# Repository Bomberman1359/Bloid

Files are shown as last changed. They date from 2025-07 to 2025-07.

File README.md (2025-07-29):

# Bloid
This is a custom, ball balancing robot. 

## CAD

Screenshot 2025-07-14 at 4 35 45 AM

## Software

Screenshot 2025-07-14 at 4 37 16 AM

## Software setup

Depending on what device you are on and what directory you export to, the first few steps could vary, so in summary: **you need to ```cd``` into the ```/Software/Main``` folder**

From there, the setup process is very simple:

Create a new python virtual environment:

```
python -m venv env
```

Enter the environment:

```
source env/bin/activate
```

Install the required packages:

```
pip install opencv-python pigpio 
```

Start up the main program:

```
#Start up the pigpio daemon
sudo pigpiod
#Main code
python main.py
```

## Wiring

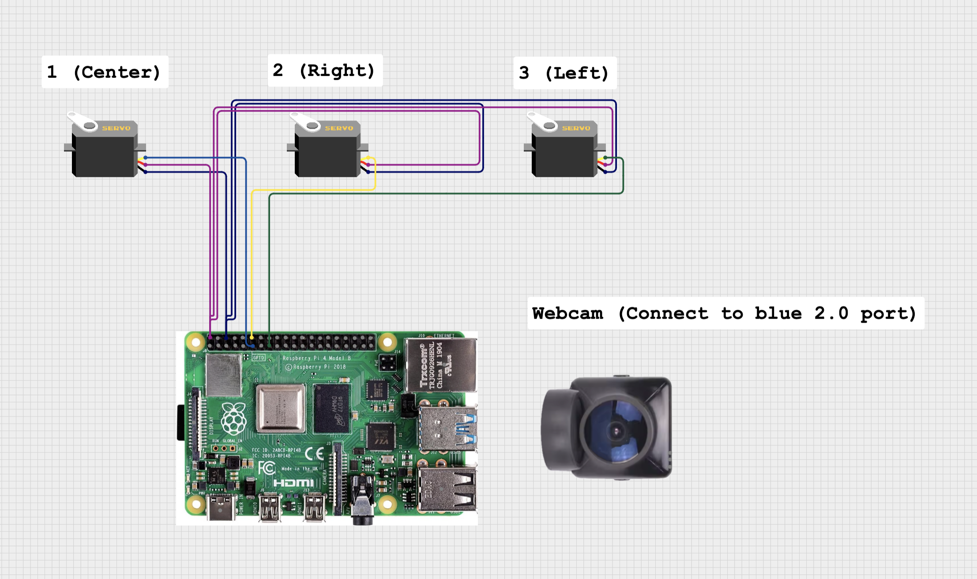
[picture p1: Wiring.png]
Wiring Diagram


## Final Product







## BOM
| Item | Quantity | Vendor | Total Price |
| :--- | :---: | :----- | ---: |
| Raspberry Pi | 1 | [PiShop USA](https://www.pishop.us/product/raspberry-pi-4-model-b-1gb/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) | $35.00 |
| Webcam |  1  |  [Walmart](https://www.walmart.com/ip/1080P-Web-Cam-HD-Camera-Webcam-with-Mic-Microphone-for-Computer-PC-Laptop-Notebook/7115471225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)| $7.99 |
| Servos Set | 1 | [Amazon](https://www.amazon.com/4-Pack-MG996R-Torque-Digital-Helicopter/dp/B07MFK266B?th=1) | $17.99 | 
| M3 Hardware (Set) | 1 | [Amazon](https://www.amazon.com/Taiss-540PCS-Stainless-Socket-Washers/dp/B0D4L6QRZB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) | $9.99 |
| Dupont Wires Set| 1 | [Amazon](https://www.amazon.com/Elegoo-EL-CP-004-Multicolored-Breadboard-arduino/dp/B01EV70C78) | $6.98 |
| 3D Printer and filaments| Undef | Undef | Undef |

Net Total Cost (Not including 3D printer/filaments): $77.95

## Link to the demo:
https://youtu.be/3Ihvu0gQJfA

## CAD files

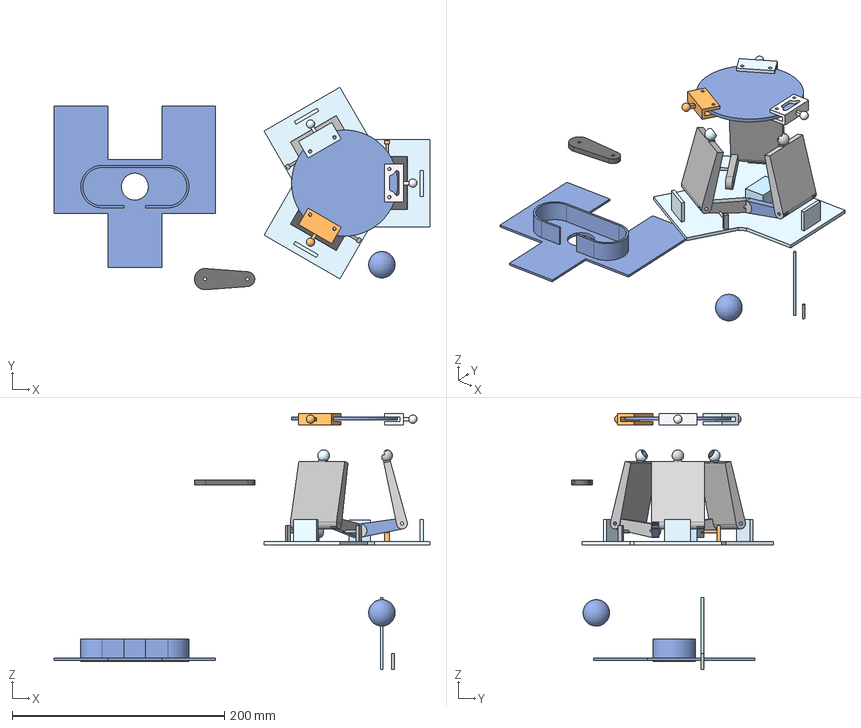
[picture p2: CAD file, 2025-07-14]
CAD/Assembly.step
354.3 x 190.8 x 241.4 mm
arm_2pad

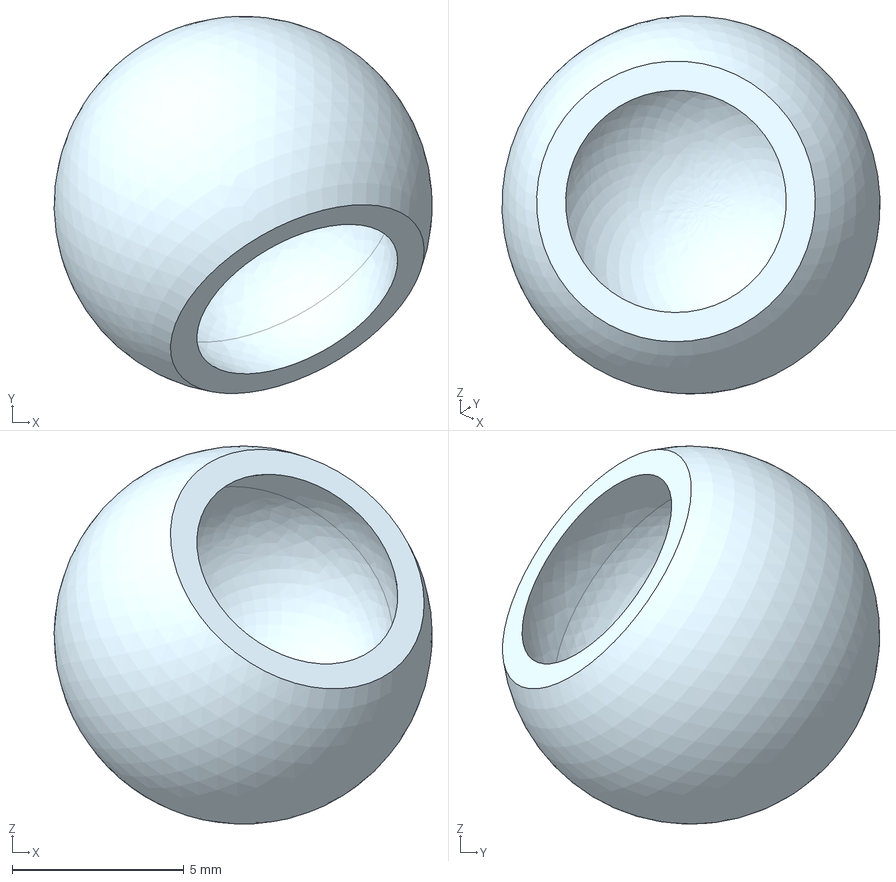
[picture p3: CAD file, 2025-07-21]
CAD/STEP/Part Studio 1 - Part 10.step
11.0 x 11.0 x 11.0 mm

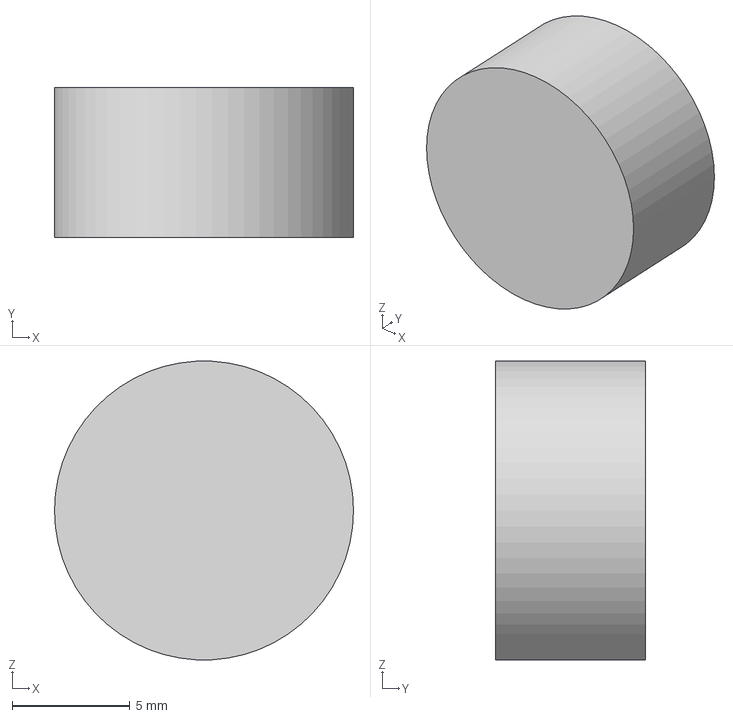
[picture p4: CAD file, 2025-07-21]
CAD/STEP/Part Studio 1 - Part 2.step
12.7 x 6.35 x 12.7 mm

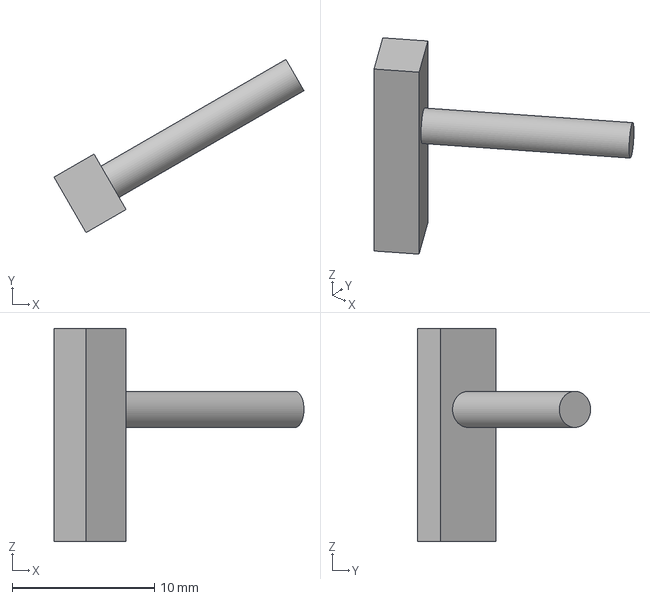
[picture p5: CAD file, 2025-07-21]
CAD/STEP/Part Studio 1 - Part 16.step
17.6 x 12.2 x 15.0 mm

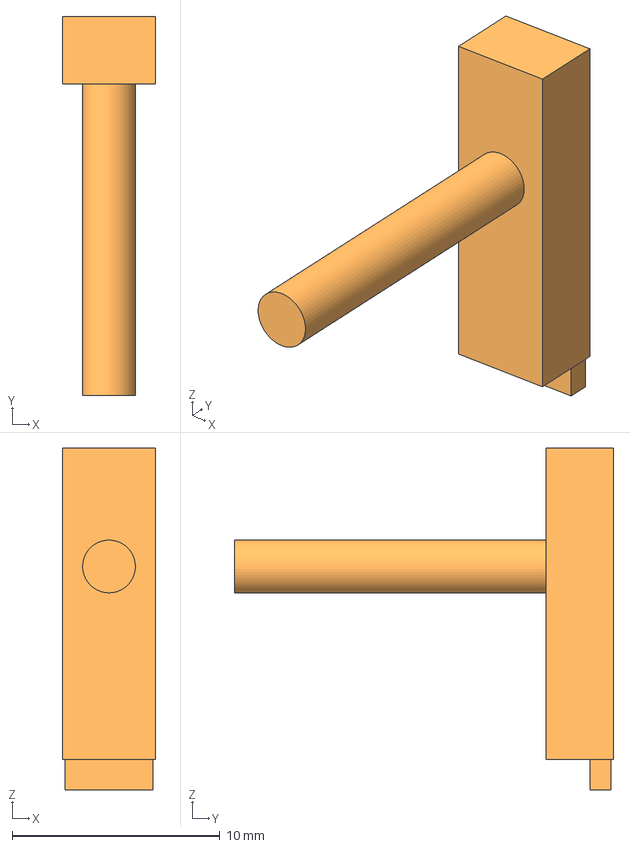
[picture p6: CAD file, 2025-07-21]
CAD/STEP/Part Studio 1 - Part 13.step
4.50 x 18.2 x 16.5 mm

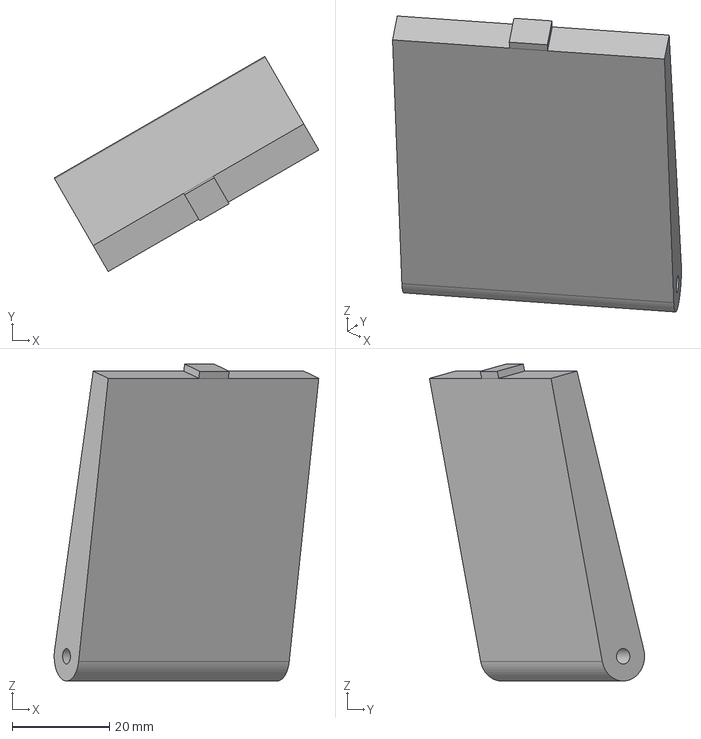
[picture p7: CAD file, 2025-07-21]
CAD/STEP/Part Studio 1 - Part 15.step
54.4 x 44.2 x 65.2 mm

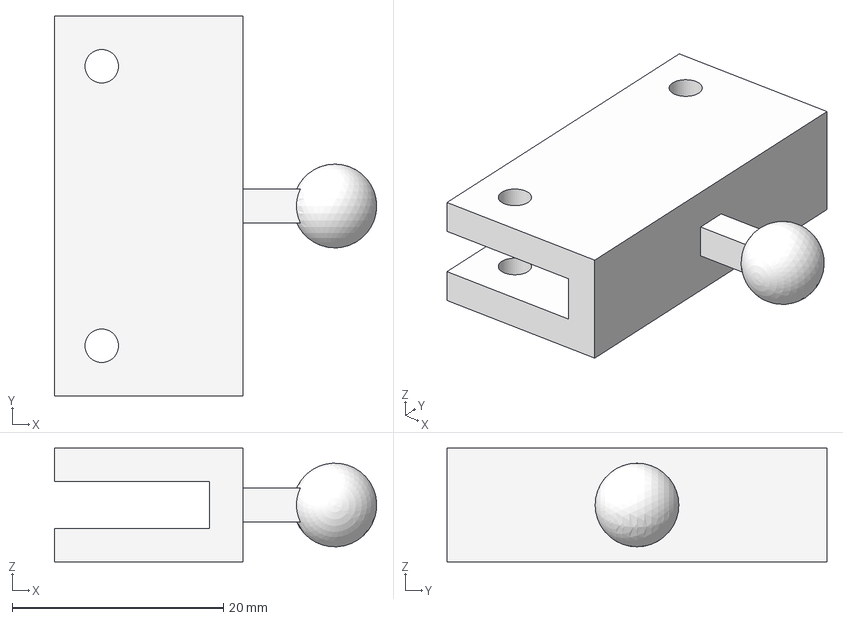
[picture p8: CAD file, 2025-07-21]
CAD/STEP/Part Studio 1 - Part 7.step
30.5 x 36.0 x 10.8 mm

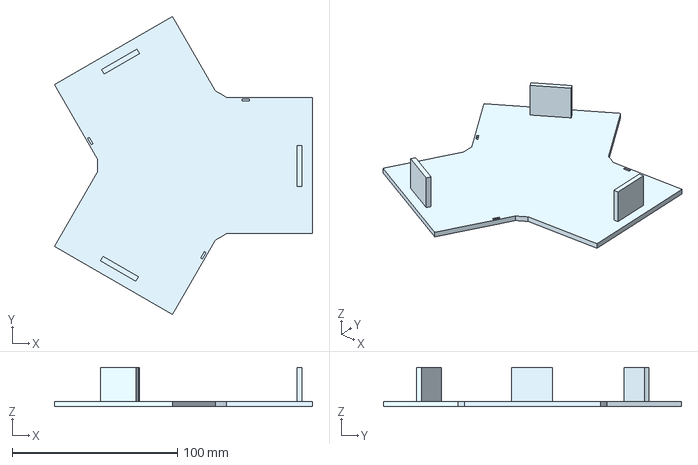
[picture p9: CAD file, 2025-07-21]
CAD/STEP/Part Studio 1 - Part 12.step
156.4 x 180.6 x 23.7 mm

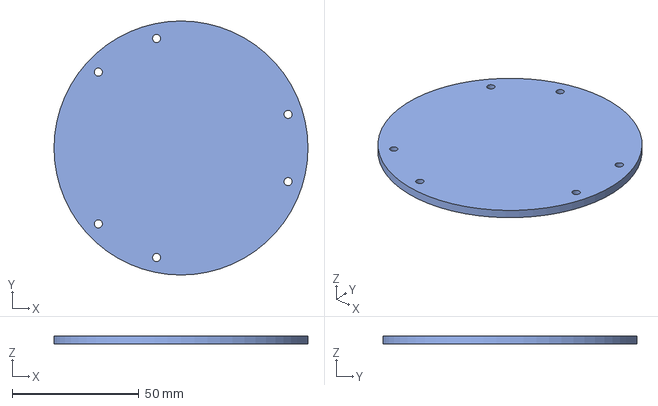
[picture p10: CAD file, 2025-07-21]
CAD/STEP/Part Studio 1 - Part 6.step
100.0 x 100.0 x 3.17 mm

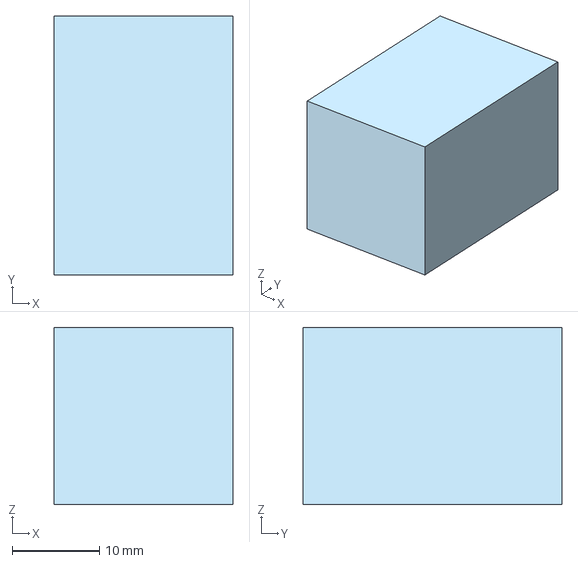
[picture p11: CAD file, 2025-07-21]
CAD/STEP/Part Studio 1 - Part 1.step
20.5 x 29.7 x 20.3 mm

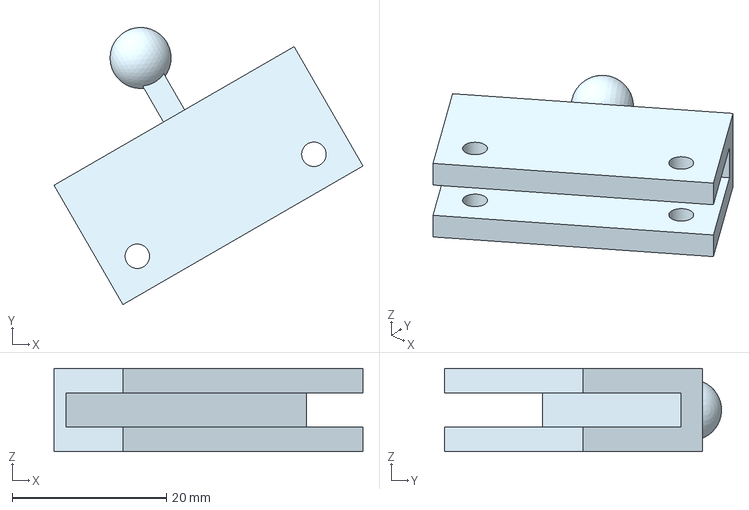
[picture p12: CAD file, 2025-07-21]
CAD/STEP/Part Studio 1 - Part 8.step
40.1 x 36.0 x 10.8 mm

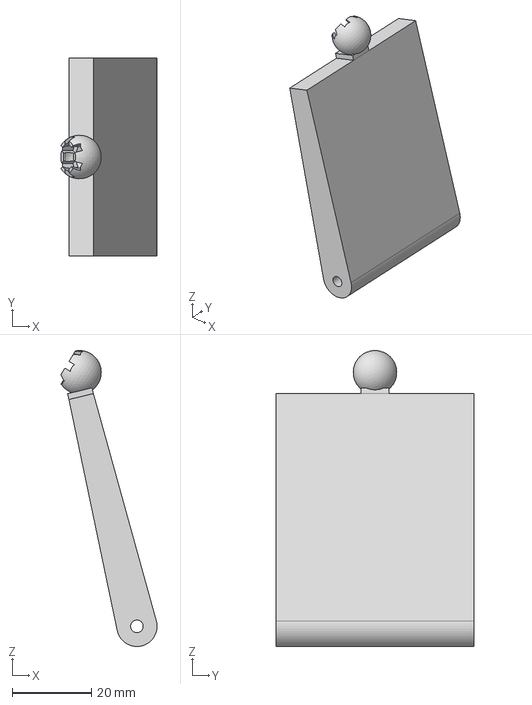
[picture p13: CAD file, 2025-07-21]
CAD/STEP/Part Studio 1 - Part 5.step
24.2 x 50.0 x 74.6 mm

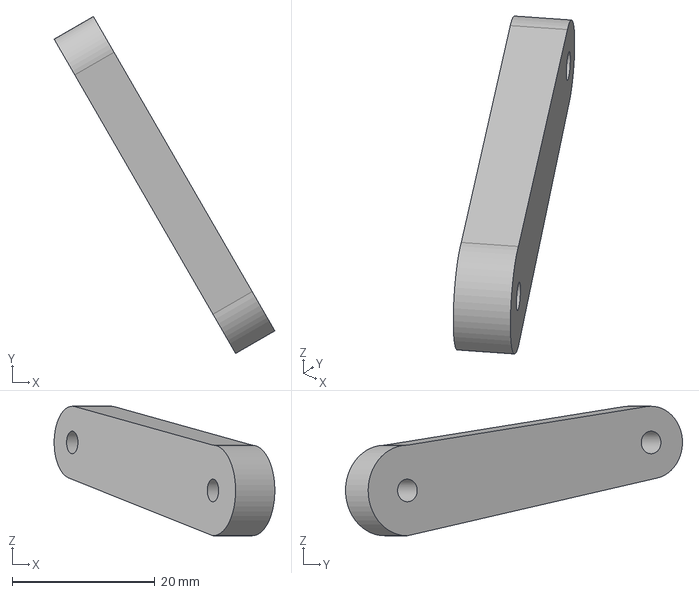
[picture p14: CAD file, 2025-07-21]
CAD/STEP/Part Studio 1 - Part 14.step
30.9 x 47.2 x 18.2 mm

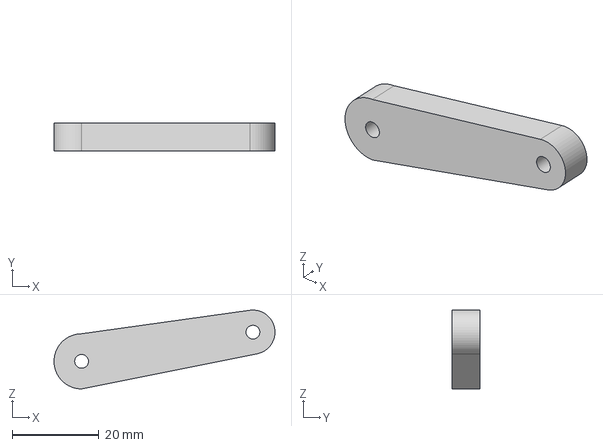
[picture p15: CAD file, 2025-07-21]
CAD/STEP/Part Studio 1 - Part 4.step
50.9 x 6.35 x 18.2 mm

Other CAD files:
CAD/STEP/Part Studio 1 - Part 19.step
CAD/STEP/Part Studio 1 - Part 11.step
CAD/STEP/Part Studio 1 - Part 18.step
CAD/STEP/Part Studio 1 - Part 9.step
CAD/STEP/Part Studio 1 - Part 17.step
CAD/STEP/Part Studio 1 - Part 3.step
CAD/STL/Part Studio 1 - Part 1.stl
CAD/STL/Part Studio 1 - Part 10.stl
CAD/STL/Part Studio 1 - Part 11.stl
CAD/STL/Part Studio 1 - Part 12.stl
CAD/STL/Part Studio 1 - Part 13.stl
CAD/STL/Part Studio 1 - Part 14.stl
CAD/STL/Part Studio 1 - Part 15.stl
CAD/STL/Part Studio 1 - Part 16.stl
CAD/STL/Part Studio 1 - Part 17.stl
CAD/STL/Part Studio 1 - Part 18.stl
CAD/STL/Part Studio 1 - Part 19.stl
CAD/STL/Part Studio 1 - Part 2.stl
CAD/STL/Part Studio 1 - Part 3.stl
CAD/STL/Part Studio 1 - Part 4.stl
CAD/STL/Part Studio 1 - Part 5.stl
CAD/STL/Part Studio 1 - Part 6.stl
CAD/STL/Part Studio 1 - Part 7.stl
CAD/STL/Part Studio 1 - Part 8.stl
CAD/STL/Part Studio 1 - Part 9.stl

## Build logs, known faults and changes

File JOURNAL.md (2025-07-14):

---
Title: "Bloid"
Author: "Chunhwee Choi, Yash Sethuramen, Jackson"
Description: "A ball balancing machine"
Created_at: "2025-07-11"
---
# Design Journal
Total Number of Hours Spent: 72 Hours

## Brainstorming and material gathering: 7/11/2025-7/12/2025, 8 Hours
At first, we had absolutely no idea what to create. It took us a while to come up with an idea, but in the end we decided to go with a ball balancing machine, which Yash and Jack remembered watching from past videos.
With an idea, we started collecting materials that we thought were necessary for the project. We first started with the huge servos, which we started with 6 of them for a 6 armed robot. 
We also gathered a bunch of wires and used Yash's raspberry pi to wire things together with a breadboard.

## CAD, Software, and Hardware: 7/12/2025 - 7/14/2025, 64 Hours
We decided to split roles. Jack would work on the CAD while Chunhwee would work on the main coding and software. Yash would do any other tasks or assist when necessary. 

### Tracking:
We decided to use a ball tracking algorithm that Yash has developed beforehand. We figured that we had to use a camera that would be mounted on a camera holder that looks at the ball from the top.
While it would have been ideal to put the camera at the bottom, we had no access to clear platforms for the camera to see through.
The way the ball tracker works is that we first take photos of the ball, remove it's background, feed it into a HSV algorithm and input the minimum and maximum HSV values into the tracking algorithm so that the camera would track that specific colored ball.

Photo on 7-13-25 at 9 09 PM #2

Photo on 7-13-25 at 6 09 PM

We had to experiment with many different colors/types of balls since the webcam quality wasn't the best, and we had a lot of trouble tracking. At first we started with a white ping pong ball, which didn't really work because white was such a common color. Then we tried pink (which the ball broke), blue (it was too shiny), and in the end we settled with red. We 3D-printed the red ball, and while the tracking wasn't perfect, with a white platform in the background, we made the tracking work out.
The tracking software would send the (x,y,z) coordinates of the ball, which would be sent to the reverse kinematics code. We had to experiment with the tracking every single day whenever we had time.

### Reverse Kinematics and PID:
To actually figure out how the platform should be balanced based on the ball's position, we had to figure out the math for reverse kinematics. While 2D reverse kinematics was doable, 3D was a whole another story.
In the end, we vibe coded the formula since it was too complicated and used test values and forward kinematics to confirm the accuracy of the math.

Screenshot 2025-07-14 at 3 05 01 AM

The image above is only a small segment of the reverse kinematics code.

For the PID, we also vibe coded. We came up with different methods to test the accuracy of the PID as well, such as creating a table of sample values to see whether the platform would move smoothly. With the PID code all set up, this will allow the servos to actually move the platform accordingly.

Screenshot 2025-07-14 at 3 05 37 AM

Another small segment of the PID code.

Reverse Kinematics and PID were created and edited throughout all days.

### CAD
Cadding the whole hardware was the most difficult part, as we had to calculate/set all the lengths and values accurately for the math in the Reverse kinematics and PID to actually work. The actual design ultimately took up until the last day, and we 3D printed each of the parts 1 at a time.

Screenshot 2025-07-14 at 3 58 52 AM

Screenshot 2025-07-14 at 2 55 12 AM

It took Jack basically 2 full days until the CAD worked out.

### Hardware
Building the hardware was the greatest strugle. The main issue was printing the ball mates, which took many different 3D printing attempts to pull of, since the PLA was  weak and the parts kept on breaking. After many adjustments, we created one that was stable enough.

For the camera mount, we ended up cutting up cardboard and created pillars, where the camera would be able to mount.









The hardwares were printed individually throughout all days.

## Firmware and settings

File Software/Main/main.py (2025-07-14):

import cv2
import time
import math
from use_test_track import find_color_mask, find_largest_contour
from use_test_PID import PID
from use_inverse_kinematics import map_xyz_to_normal, kinema_inv
from use_test_servo import SERVO_PINS, pigpio, MIN_PULSE_WIDTH, MAX_PULSE_WIDTH

"""
Main loop for ball balancing robot
 Detects ball position
 Computes PID control
 Uses inverse kinematics to get servo angles
 Moves servos accordingly
"""

# Initialize camera
camera = cv2.VideoCapture(0)
if not camera.isOpened():
    raise RuntimeError("Error: Could not open camera.")
time.sleep(2)

K_PID = [1.0, 0.1, 0.05]  # Tune these values for your robot
k = 1.0
alpha = 0.5
pid = PID(K_PID, k, alpha)

pi = pigpio.pi()
if not pi.connected:
    raise RuntimeError("Failed to connect to pigpio daemon.")
for pin in SERVO_PINS:
    pi.set_mode(pin, pigpio.OUTPUT)

try:
    while True:
        ret, frame = camera.read()
        if not ret or frame is None:
            print("Error: Frame not captured")
            break

        mask = find_color_mask(frame)
        x, y, radius, center = find_largest_contour(mask)

        frame_center = (frame.shape[1] // 2, frame.shape[0] // 2)
        goal = frame_center
        current_value = center

        # PID calculation
        theta, phi = pid.compute(goal, current_value)

        # Convert PID output to platform tilt (x, y)
        tilt_x = phi * math.cos(math.radians(theta)) / 100.0
        tilt_y = phi * math.sin(math.radians(theta)) / 100.0

        # Kinematics: get servo angles
        normal = map_xyz_to_normal(tilt_x, tilt_y, 0)
        Pz = 0.0632  # Platform height, tune for your robot
        servo_angles = kinema_inv(normal, Pz)

        # Move servos (mapping from angles to pulsewidths, clamped)
        for i, angle in enumerate(servo_angles):
            # Clamp angle between 0 and 180
            angle = max(0, min(180, float(angle)))
            pulsewidth = int(MIN_PULSE_WIDTH + (MAX_PULSE_WIDTH - MIN_PULSE_WIDTH) * (angle / 180))
            pulsewidth = max(MIN_PULSE_WIDTH, min(MAX_PULSE_WIDTH, pulsewidth))
            pi.set_servo_pulsewidth(SERVO_PINS[i], pulsewidth)

        cv2.imshow("Tracking", frame)
        if cv2.waitKey(1) & 0xff == ord('q'):
            break
finally:
    # Cleanup
    for pin in SERVO_PINS:
        pi.set_servo_pulsewidth(pin, 0)
    pi.stop()
    cv2.destroyAllWindows()
    camera.release()

# Cleanup
for pin in SERVO_PINS:
    pi.set_servo_pulsewidth(pin, 0)
pi.stop()
cv2.destroyAllWindows()
camera.release()

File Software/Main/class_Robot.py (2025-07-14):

import class_servo as cs
import math
import time

class BBrobot:
    # Create the structure of the robot
    def __init__(self, gpio_pins):  # Receive a list of GPIO pins
        # Prepare the servos
        self.s1 = cs.RS304MD(gpio_pins[0])
        self.s2 = cs.RS304MD(gpio_pins[1])
        self.s3 = cs.RS304MD(gpio_pins[2])
        # Link lengths L = [base, lower link, upper link, top]
        self.L = [0.04, 0.04, 0.065, 0.065]
        # Initial posture (theta, phi, pz)
        self.ini_pos = [0, 0, 0.0632]
        self.pz_max = 0.0732
        self.pz_min = 0.0532
        self.phi_max = 20

    # Method to prepare the robot
    def set_up(self):
        # Turn on the torque of the servos
        self.s1.trq_set(1)
        self.s2.trq_set(1)
        self.s3.trq_set(1)
        
    # Method to clean up the robot
    def clean_up(self):
        # Turn off the torque of the servos
        self.s1.trq_set(0)
        self.s2.trq_set(0)
        self.s3.trq_set(0)
        # Cleanup pigpio resources
        self.s1.cleanup()
        self.s2.cleanup()
        self.s3.cleanup()

    # Method to calculate inverse kinematics
    def kinema_inv(self, n, Pz):
        L = self.L
        # Derive the height Pmz at the servo reference (reverse sign with Pmz)
        A = (L[0]+L[1])/Pz
        B = (Pz**2+L[2]**2-(L[0]+L[1])**2-L[3]**2)/(2*Pz)
        C = A**2+1
        D = 2*(A*B-(L[0]+L[1]))
        E = B**2+(L[0]+L[1])**2-L[2]**2
        Pmx = (-D+math.sqrt(D**2-4*C*E))/(2*C)
        Pmz = math.sqrt(L[2]**2-Pmx**2+2*(L[0]+L[1])*Pmx-(L[0]+L[1])**2)

        # Derive the angle of servo a
        a_m_x = (L[3]/(math.sqrt(n[0]**2 + n[2]**2)))*(n[2])
        a_m_y = 0
        a_m_z = Pz + (L[3]/(math.sqrt(n[0]**2 + n[2]**2)))*(-n[0])
        A_m = [a_m_x, a_m_y, a_m_z]
        A = (L[0]-A_m[0])/A_m[2]
        B = (A_m[0]**2+A_m[1]**2+A_m[2]**2-L[2]**2-L[0]**2+L[1]**2)/(2*A_m[2])
        C = A**2+1
        D = 2*(A*B-L[0])
        E = B**2+L[0]**2-L[1]**2
        ax = (-D+math.sqrt(D**2-4*C*E))/(2*C)
        ay = 0
        az = math.sqrt(L[1]**2-ax**2+2*L[0]*ax-L[0]**2)
        if (a_m_z < Pmz):
            az = -az
        A_2 = [ax, ay, az]
        theta_a = 90 - math.degrees(math.atan2(A_2[0]-L[0], A_2[2]))

        # Derive the angle of servo b
        b_m_x = (L[3]/(math.sqrt(n[0]**2+3*n[1]**2+4*n[2]**2+2*math.sqrt(3)*n[0]*n[1])))*(-n[2])
        b_m_y = (L[3]/(math.sqrt(n[0]**2+3*n[1]**2+4*n[2]**2+2*math.sqrt(3)*n[0]*n[1])))*(-math.sqrt(3)*n[2])
        b_m_z = Pz + (L[3]/(math.sqrt(n[0]**2+3*n[1]**2+4*n[2]**2+2*math.sqrt(3)*n[0]*n[1])))*(math.sqrt(3)*n[1]+n[0])
        B_m = [b_m_x, b_m_y, b_m_z]

        A = -(B_m[0]+math.sqrt(3)*B_m[1]+2*L[0])/B_m[2]
        B = (B_m[0]**2+B_m[1]**2+B_m[2]**2+L[1]**2-L[2]**2-L[0]**2)/(2*B_m[2])
        C = A**2+4
        D = 2*A*B+4*L[0]
        E = B**2+L[0]**2-L[1]**2
        x = (-D-math.sqrt(D**2-4*C*E))/(2*C)
        y = math.sqrt(3)*x
        z = math.sqrt(L[1]**2-4*x**2-4*L[0]*x-L[0]**2)
        if (b_m_z < Pmz):
            z = -z
        B_2 = [x, y, z]
        theta_b = 90 - math.degrees(math.atan2(math.sqrt(B_2[0]**2+B_2[1]**2)-L[0], B_2[2]))

        # Derive the angle of servo c
        c_m_x = (L[3]/(math.sqrt(n[0]**2+3*n[1]**2+4*n[2]**2-2*math.sqrt(3)*n[0]*n[1])))*(-n[2])
        c_m_y = (L[3]/(math.sqrt(n[0]**2+3*n[1]**2+4*n[2]**2-2*math.sqrt(3)*n[0]*n[1])))*(math.sqrt(3)*n[2])
        c_m_z = Pz + (L[3]/(math.sqrt(n[0]**2+3*n[1]**2+4*n[2]**2-2*math.sqrt(3)*n[0]*n[1])))*(-math.sqrt(3)*n[1]+n[0])
        C_m = [c_m_x, c_m_y, c_m_z]

        A = -(C_m[0]-math.sqrt(3)*C_m[1]+2*L[0])/C_m[2]
        B = (C_m[0]**2+C_m[1]**2+C_m[2]**2+L[1]**2-L[2]**2-L[0]**2)/(2*C_m[2])
        C = A**2+4
        D = 2*A*B+4*L[0]
        E = B**2+L[0]**2-L[1]**2
        x = (-D-math.sqrt(D**2-4*C*E))/(2*C)
        y = -math.sqrt(3)*x
        z = math.sqrt(L[1]**2-4*x**2-4*L[0]*x-L[0]**2)
        if (c_m_z < Pmz):
            z = -z
        C_2 = [x, y, z]
        theta_c = 90 - math.degrees(math.atan2(math.sqrt(C_2[0]**2+C_2[1]**2)-L[0], C_2[2]))
        thetas = [theta_a, theta_b, theta_c]
        return thetas

    # Method to achieve posture (theta, phi, Pz) after t seconds
    def control_t_posture(self, pos, t):
        theta = pos[0]
        phi = pos[1]
        # Motion constraints
        if phi > self.phi_max:
            phi = self.phi_max
        Pz = pos[2]
        if Pz > self.pz_max:
            Pz = self.pz_max
        elif Pz < self.pz_min:
            Pz = self.pz_min 
        z = math.cos(math.radians(phi))
        r = math.sin(math.radians(phi))
        x = r*math.cos(math.radians(theta))
        y = r*math.sin(math.radians(theta))
        n = [x, y, z]
        angles = self.kinema_inv(n, Pz)
        self.s1.control_time_rotate(angles[0], t)
        self.s2.control_time_rotate(angles[1], t)
        self.s3.control_time_rotate(angles[2], t)
        time.sleep(t)
    
    def initialize_posture(self):
        pos = self.ini_pos
        t = 1
        self.control_t_posture(pos, t)

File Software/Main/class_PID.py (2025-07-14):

import math
import time

class PID:
    def __init__(self, K_PID, k, alpha):
        self.kp = K_PID[0]  # Proportional gain
        self.ki = K_PID[1]  # Integral gain
        self.kd = K_PID[2]  # Derivative gain
        self.k = k  # Scaling factor
        self.alpha = alpha  # Coefficient for the low-pass filter
        self.last_output_x = 0
        self.last_output_y = 0
        self.last_error_x = 0
        self.integral_x = 0
        self.last_error_y = 0
        self.integral_y = 0
        self.last_time = None
        self.count = 0
        self.F = 0

    def compute(self, Goal, Current_value):
        current_time = time.perf_counter()
        if self.last_time is None:
            self.last_time = current_time
            return 0, 0
        # Calculate error
        error_x = Goal[0] - Current_value[0]
        error_y = Goal[1] - Current_value[1]
        # Calculate integral term
        self.integral_x += error_x * (current_time - self.last_time)
        self.integral_y += error_y * (current_time - self.last_time)
        # Calculate derivative term
        derivative_x = (error_x - self.last_error_x) / (current_time - self.last_time)
        derivative_y = (error_y - self.last_error_y) / (current_time - self.last_time)
        # Calculate PID output
        output_x = self.kp * error_x + self.ki * self.integral_x + self.kd * derivative_x
        output_y = self.kp * error_y + self.ki * self.integral_y + self.kd * derivative_y
        # Apply low-pass filter
        output_x = self.alpha * output_x + (1 - self.alpha) * self.last_output_x
        output_y = self.alpha * output_y + (1 - self.alpha) * self.last_output_y
        # Calculate theta and phi
        theta = math.degrees(math.atan2(output_y, output_x))
        if theta < 0:
            theta += 360
        phi = self.k * math.sqrt(output_x**2 + output_y**2)

        self.last_error_x = error_x
        self.last_error_y = error_y
        self.last_output_x = output_x
        self.last_output_y = output_y
        self.last_time = current_time

        return theta, phi

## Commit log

2025-07-14 Add software
    [pid_log.csv]
2025-07-21 Add parts
    [Assembly.step, Part Studio 1 - Part 1.step, Part Studio 1 - Part 1.stl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]
